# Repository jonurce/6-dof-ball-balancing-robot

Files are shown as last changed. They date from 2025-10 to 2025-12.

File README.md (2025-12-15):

# 6 Degree-of-Freedom Ball Balancing Robot 

**This project was developed as part of the course MMA4004 Mechatronics and Systems Integrations at NTNU, Ålesund**

**It was also done as a part time job, which focused on creating a reproducible project for robotics students at NTNU**

version-1
version-1-1

## Overview

This repository shows the building process of a 6 degree-of-freedom ball balancing robot. It can be used as a learning project for robotics students, as it was used for Master students in Mechatronics and Automation at NTNU, Ålesund.

## Repository Description

The repository is divided as follows:

```     
├── Arduino Code                                            # Arduino code, including the solved and not-solved versions 
├── Arduino libraries                                       # Manually installed Arduino libraries  
├── CAD files                                               # 3D files in STL format, ready for 3D printing
├── Lasercuted files                                        # Drawings for lasercuting components
├── Final Version                                           # Final version of the project for the course MMA4004
├── 6 DOF Ball Balancing Robot - Guide.pdf                  # Step by step guide to build the platform
├── 6 DOF Ball Balancing Robot - Inverse Kinematics.pdf     # Inverse Kinematics solution explanation
└── List of Materials.xlsx                                  # Component list with links
```

## Project for students

If using this repository as a project for students, it is proposed to not provide the inverse kinematics solution `6 DOF Ball Balancing Robot - Inverse Kinematics.pdf` neither the solved arduino code `Arduino Code/Arduino_Code_Solved` nor the final version `Final Version`. In addition, the document `6 DOF Ball Balancing Robot - Guide.pdf` was explicitly made for students to follow.

## Final version of the project for MMA4004

version-2
version-2-1

The final version presented for the course is available at the folder `Final Version`, which is distributed as follows:

```     
├── Final Version                                           
    ├── Code                                            # Final code
    ├── CAD_files.zip                                   # CAD files including first and second version STL files for 3D printing and drawings for lasercuting
    └── Final Report - 6 DOF Ball Balancing Robot.pdf   # Final project report
```

The final project report `Final Version/Final Report - 6 DOF Ball Balancing Robot.pdf` explains all the implemented features in detail, as well as the obtained results.

The final code is explained in details at Modesta's repository: https://github.com/ModeS7/MMA4004-stewart.git

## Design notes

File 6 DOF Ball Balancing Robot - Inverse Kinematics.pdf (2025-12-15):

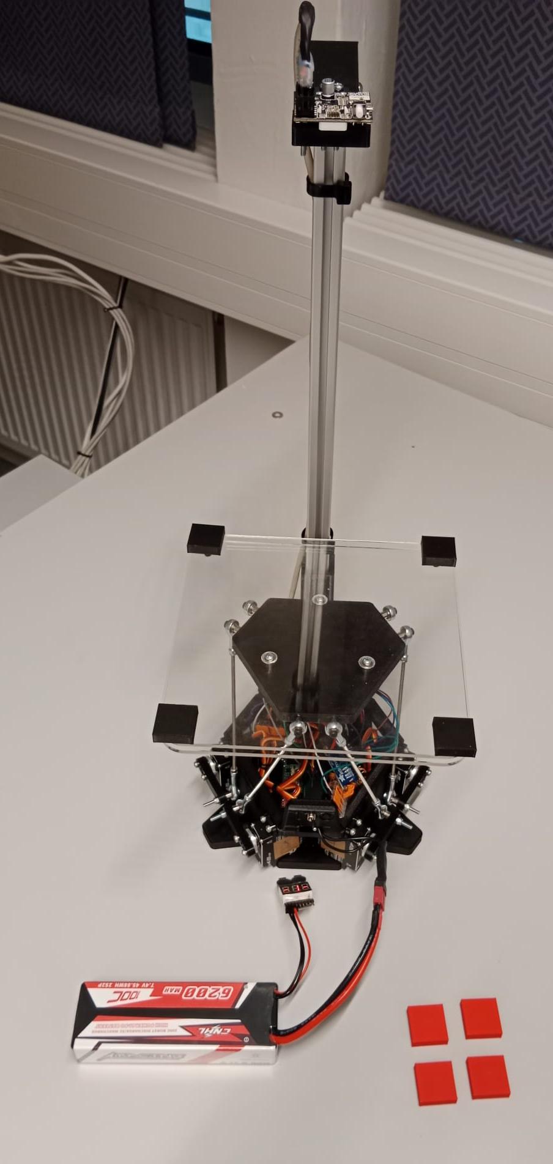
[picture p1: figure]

## 6-Degree-of-Freedom Ball Balancing Robot

Inverse Kinematics (IK)

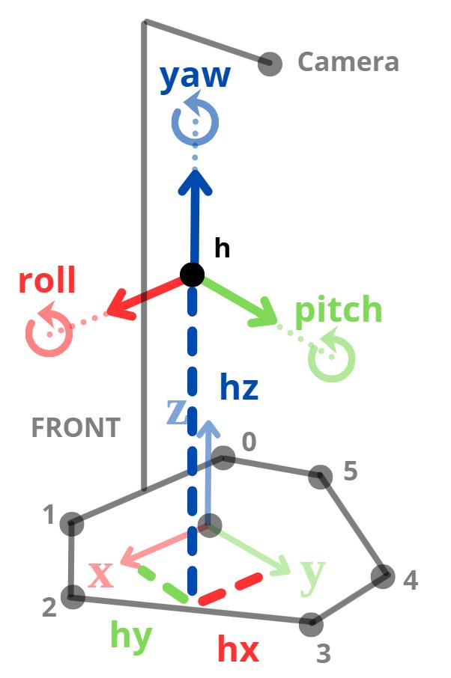
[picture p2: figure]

## IK main objetive

Given a desired h point:
h = {hx, hy, hz, roll, pitch, yaw}

Find x6 motor angles:
angles = {0, 1, 2, 3, 4, 5}

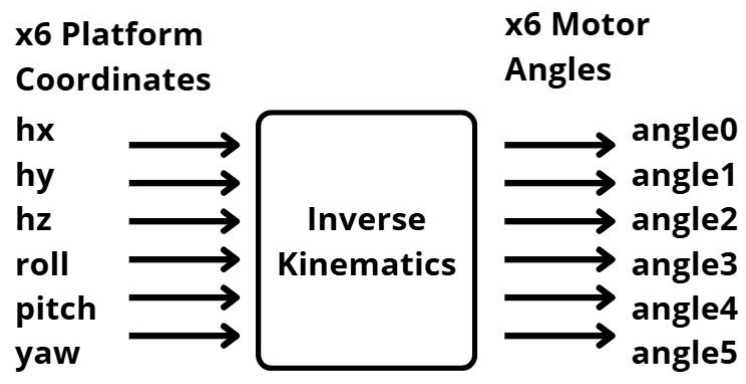
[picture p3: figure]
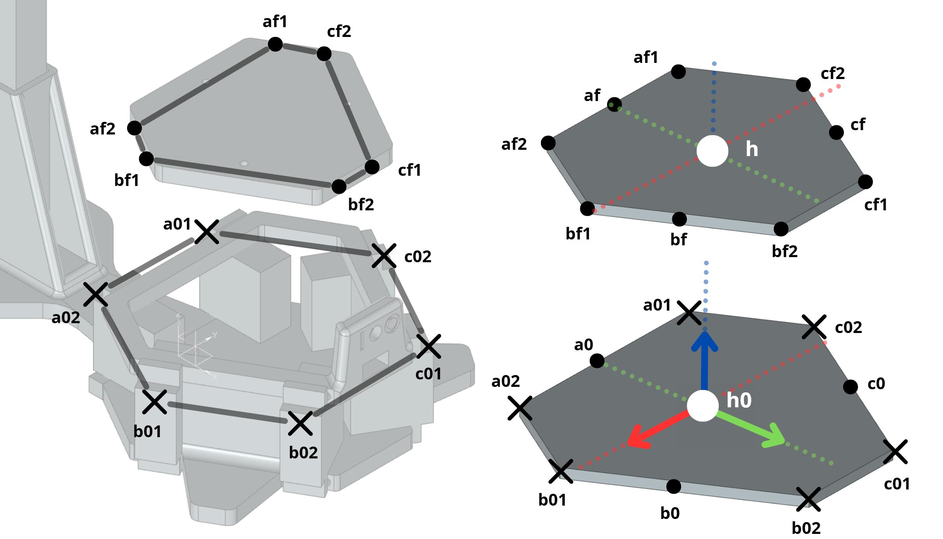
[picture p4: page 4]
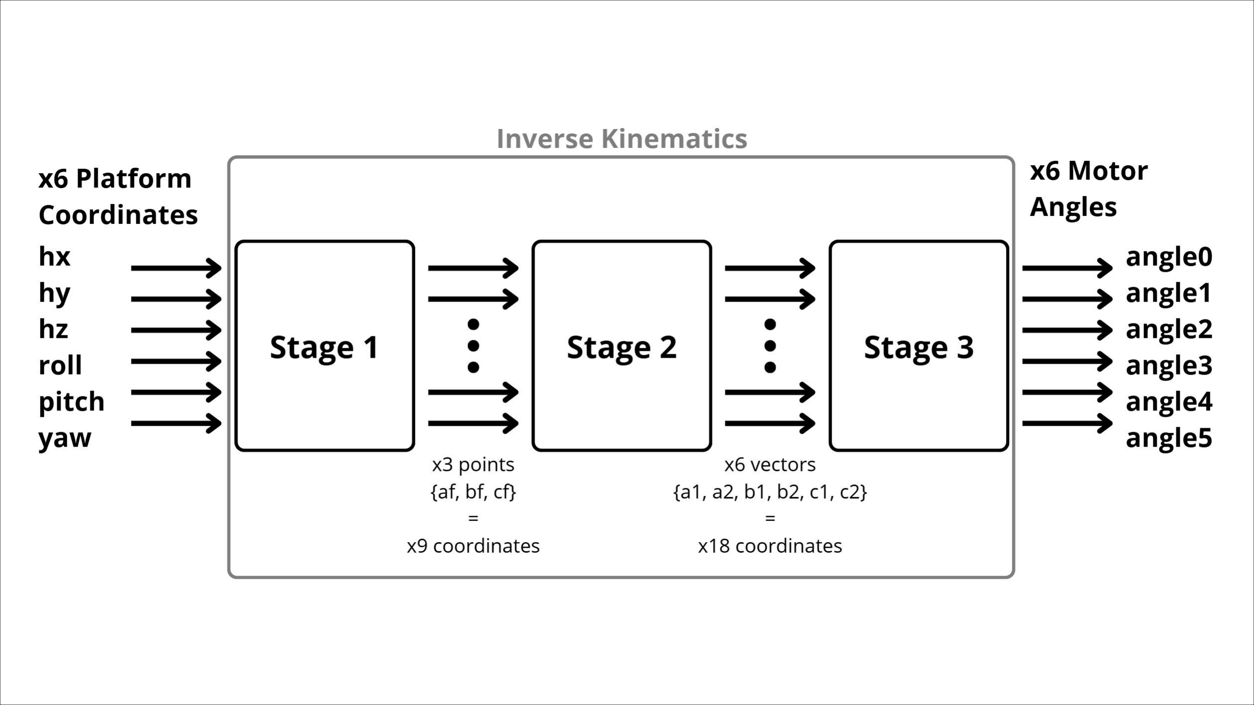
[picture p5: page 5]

## Stage 1: from h to {af, bf, cf}

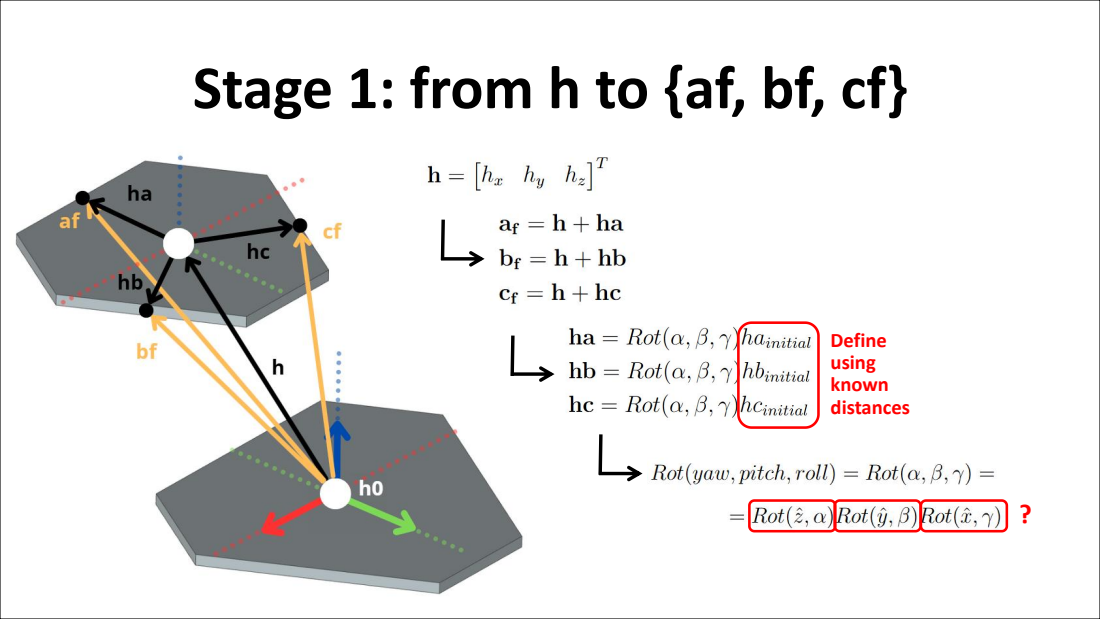
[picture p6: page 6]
Define using known distances

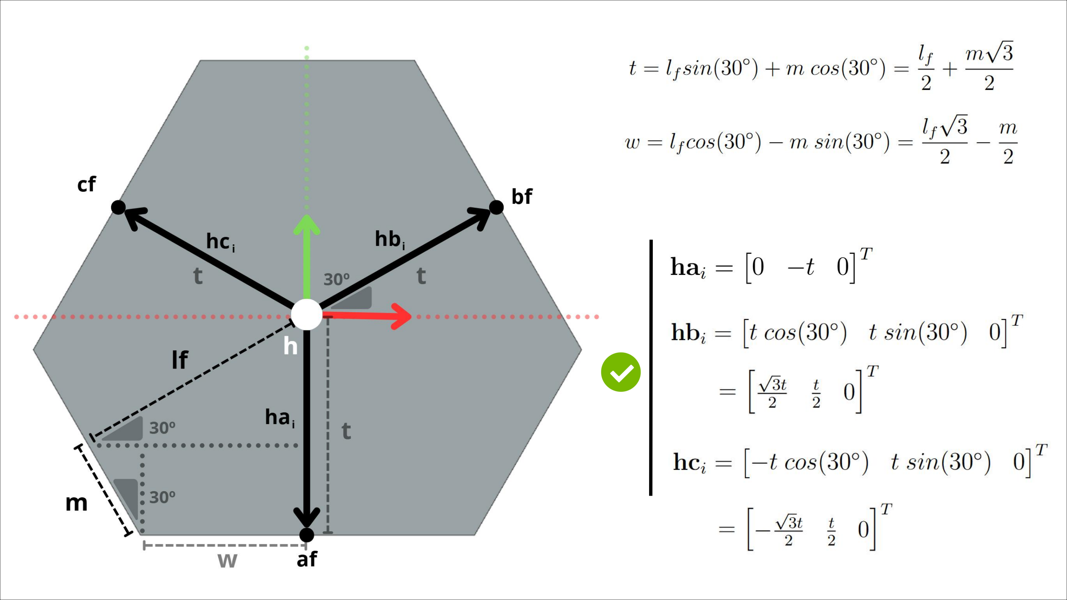
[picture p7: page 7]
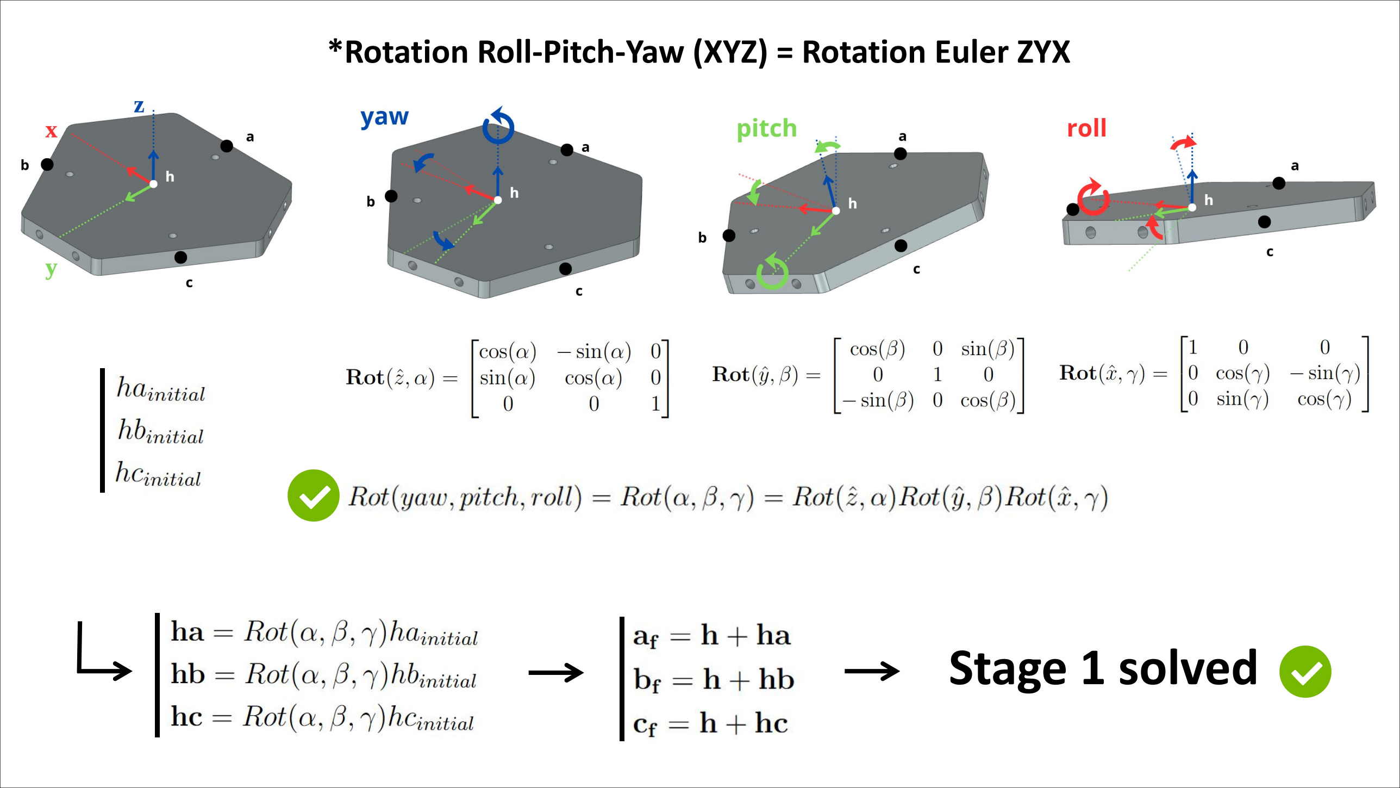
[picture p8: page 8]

Stage 1 solved

*Rotation Roll-Pitch-Yaw (XYZ) = Rotation Euler ZYX

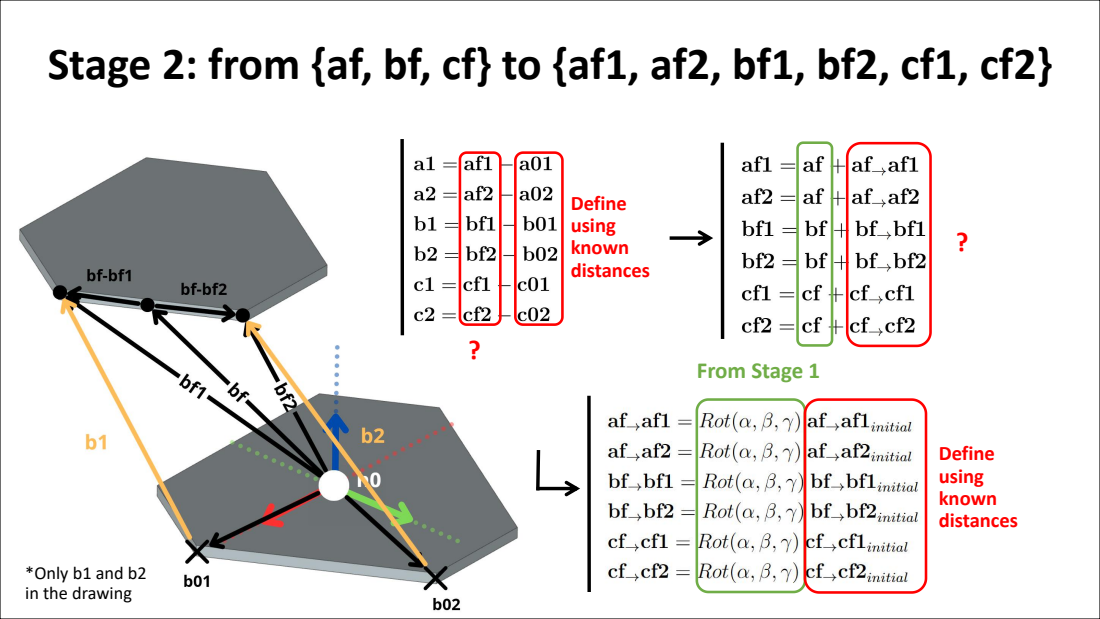
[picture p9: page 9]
From Stage 1; Define using known distances

Stage 2: from {af, bf, cf} to {af1, af2, bf1, bf2, cf1, cf2}

*Only b1 and b2
in the drawing

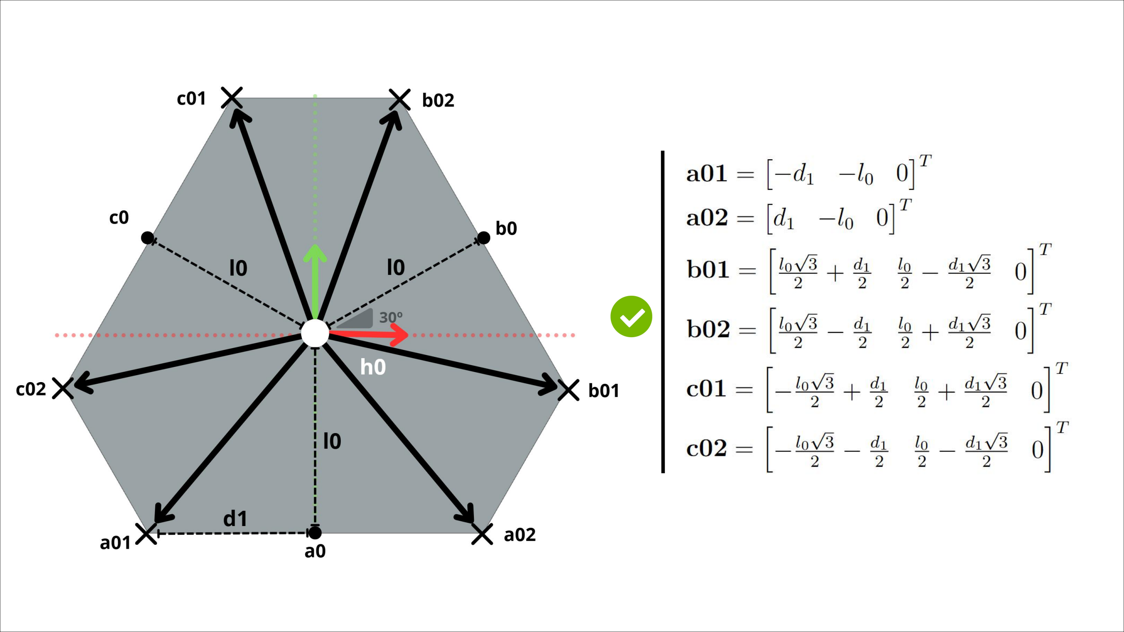
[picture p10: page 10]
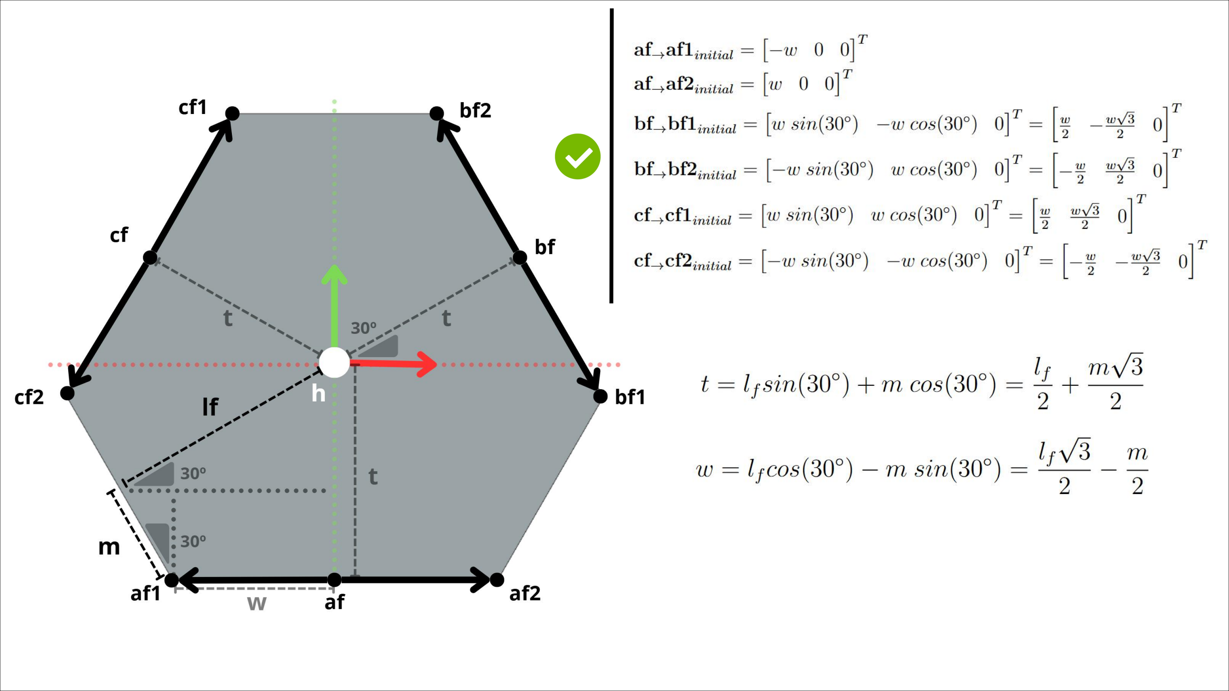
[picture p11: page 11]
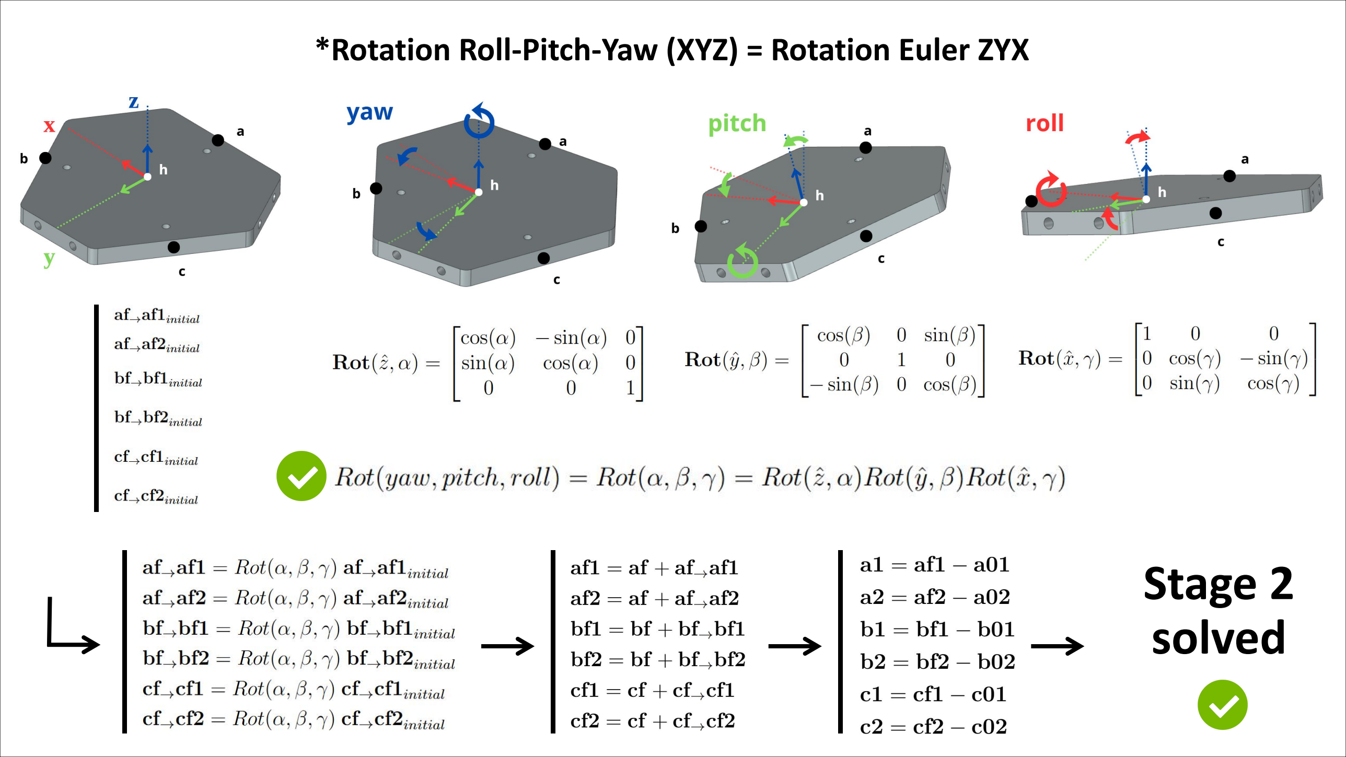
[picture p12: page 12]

*Rotation Roll-Pitch-Yaw (XYZ) = Rotation Euler ZYX

Stage 2
solved

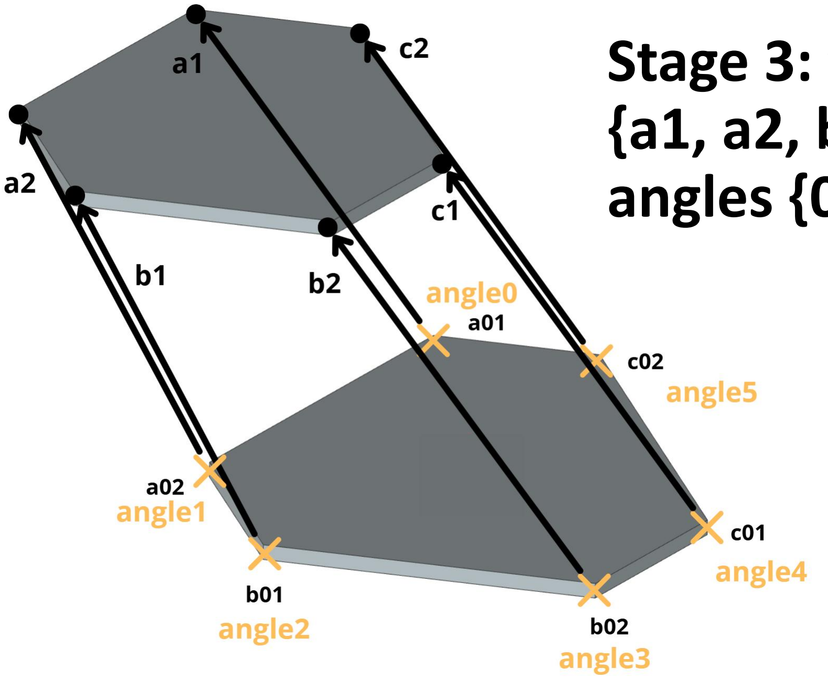
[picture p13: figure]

Stage 3: from vectors
{a1, a2, b1, b2, c1, c2} to angles {0, 1, 2, 3, 4, 5}

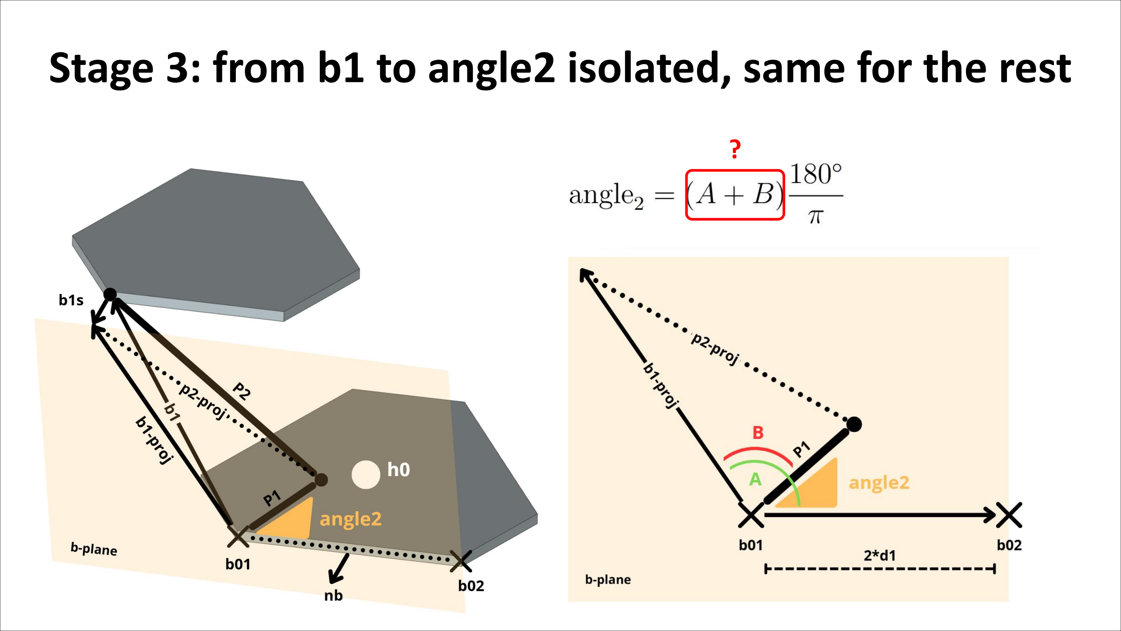
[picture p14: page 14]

Stage 3: from b1 to angle2 isolated, same for the rest

?

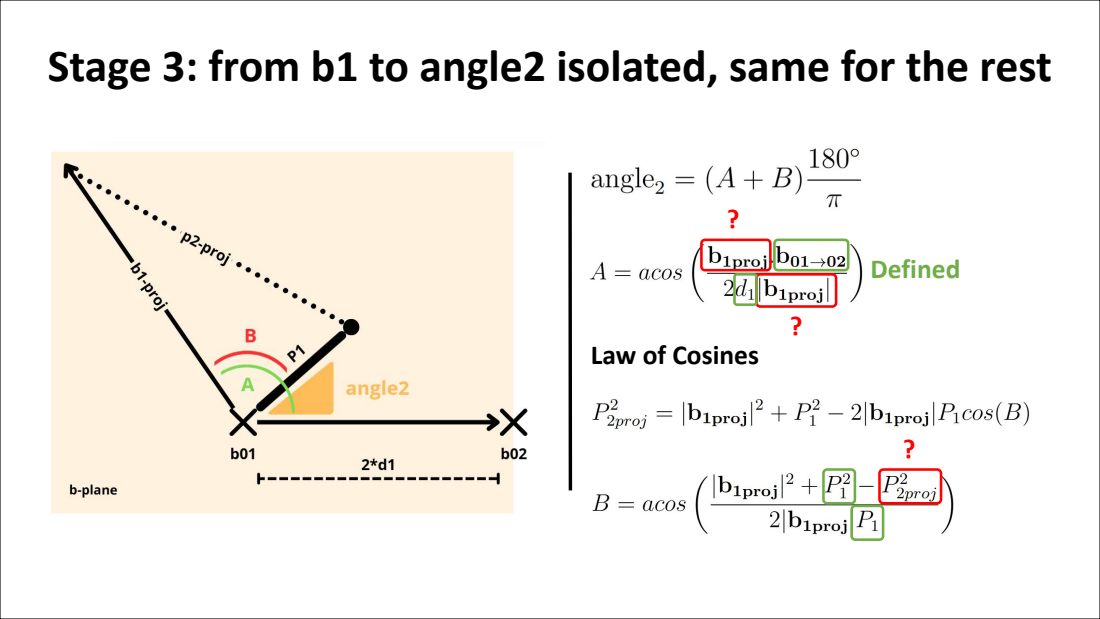
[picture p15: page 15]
Defined

Stage 3: from b1 to angle2 isolated, same for the rest

Law of Cosines

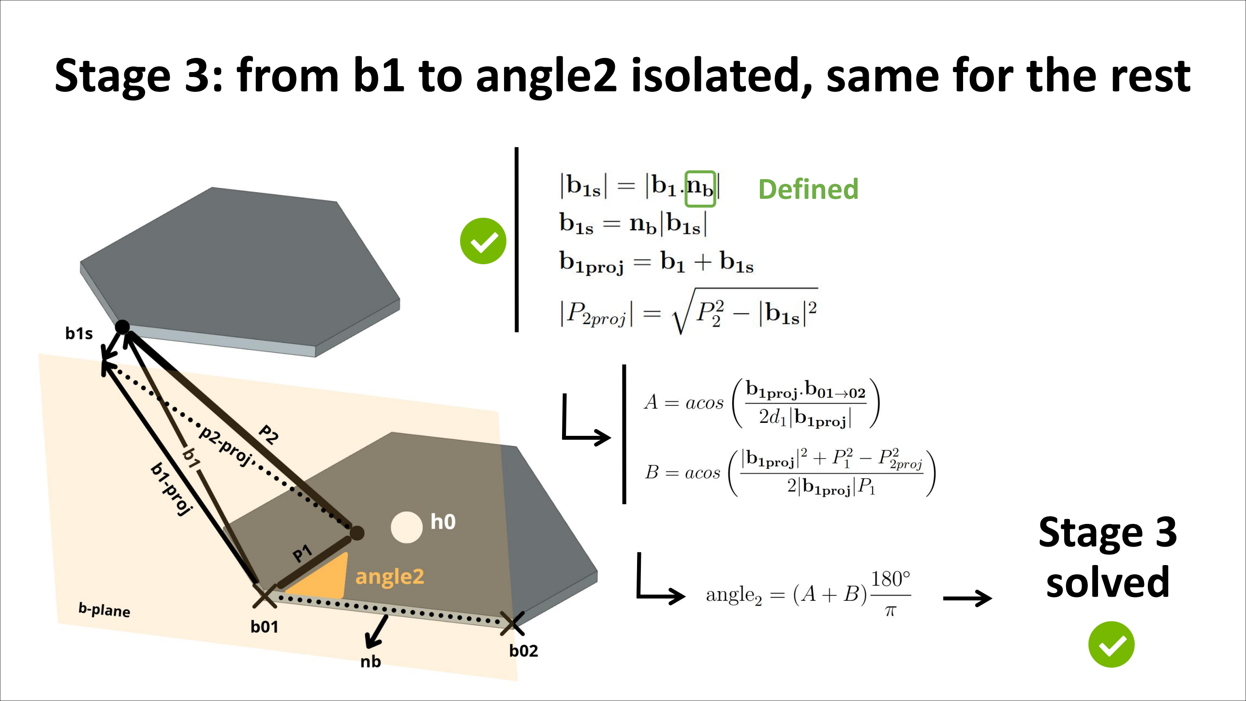
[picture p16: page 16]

Stage 3: from b1 to angle2 isolated, same for the rest

Stage 3
solved

Defined

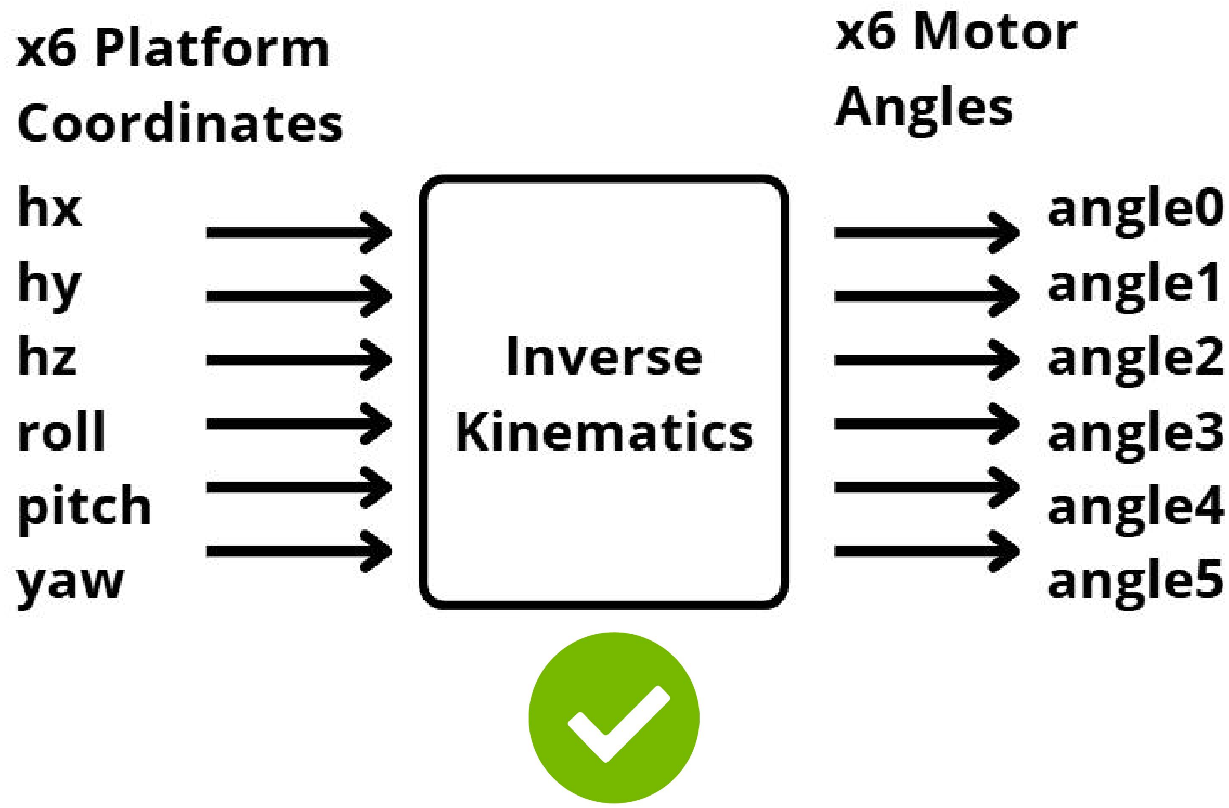
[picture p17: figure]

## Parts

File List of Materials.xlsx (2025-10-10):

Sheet: Bill of Materials
6 DOF Platform - List of components
Electronics | Units | Materials | Units
Servo Motor 20Kg 7.4V (https://www.digikey.no/en/products/detail/dfrobot/SER0030/7597225) | 6 | 3D printer filament | -
Teensy 4.1 (https://www.elfadistrelec.no/en/teensy-development-board-6v-sparkfun-electronics-dev-16771/p/30178274) | 1 | Acrylic 3mm thickness | -
Micro Maestro 6-channel USB Servo Controller (https://www.digikey.no/no/products/detail/sparkfun-electronics/09664/5764499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) | 1 | Aluminium Servo Disc | 6
Pixy 2 Camera (https://www.elfadistrelec.no/en/pixy2-cmucam5-camera-board-sparkfun-electronics-sen-14678/p/30145515) | 1 | M3 Stainless Steel Threaded Rod 1m (https://no.rs-online.com/web/p/threaded-rods/0280363) | 1
3.3V to 5V LLC (https://www.elfadistrelec.no/en/bi-directional-logic-voltage-level-converter-sparkfun-electronics-bob-12009/p/30145425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) | 1 | M3 x 6mm Inserts (https://no.rs-online.com/web/p/threaded-inserts/2040620?gb=s) | 48
Custom PCB (https://www.pcbway.com/) | 1 | M3 x 5mm Standoff (https://no.rs-online.com/web/p/standoffs/0222367?gb=s) | 22
Male Pins 1 Row for PCB (https://no.rs-online.com/web/p/pcb-headers/7671176P?gb=s) | 84 | M3 Locknuts (https://no.rs-online.com/web/p/hex-nuts/0767804?gb=s) | 24
Female Pins 1 Row for PCB (https://no.rs-online.com/web/p/pcb-sockets/7655806?gb=s) | 80 | M3 x 5mm Screws (https://no.rs-online.com/web/p/socket-screws/8229094?gb=s) | 24
Male-female/male-male wire | 6 | M3 x 14mm Screws (https://no.rs-online.com/web/p/socket-screws/0606457?gb=s) | 30
2-Contact Screw Termination (https://no.rs-online.com/web/p/pcb-terminal-blocks/1468345?gb=s) | 1 | M3 x 20mm Button Head Screw (https://no.rs-online.com/web/p/security-screws/6212760?gb=s) | 3
USB cable | 2 | M3 x 25mm Screw (https://no.rs-online.com/web/p/socket-screws/0293319?gb=s) | 9
3x2 Male Pins (https://no.rs-online.com/web/p/pcb-headers/1802895) | 1 | 20 x 20mm Alum Profile 5mm Groove 2m (https://no.rs-online.com/web/p/tubing-and-profile-struts/8508470?gb=s) | 1.2
3x2 Female Pins (https://no.rs-online.com/web/p/pcb-sockets/2079182?gb=s) | 2 | M5 T-Slot Nut Groove Size 5mm (https://no.rs-online.com/web/p/connecting-components/1809104) | 8
Toggle Switch (https://www.elfadistrelec.no/en/miniature-toggle-switch-on-off-on-1co-soldering-lugs-rs-pro-7347123/p/30466736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) | 1 | M5 x 12mm Screw (https://no.rs-online.com/web/p/socket-screws/0281079?gb=s) | 8
18 AWG Wire | 40cm | Silicon Glue Tube (https://no.rs-online.com/web/p/glues/7703434?gb=s) | 1
Amass T-Plug2 [deans] - 1x Male (https://www.elkjop.no/product/hjem-rengjoring-og-kjokkenutstyr/belysning-og-elektriske-artikler/elektrisk-utstyr/kabler-og-adaptere/amass-t-plug2-deans-1x-mal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) | 1
LiPo Battery 7.4V 6200mAh (https://www.elkjop.no/product/sport-hobby-og-fritid/leker/radiostyrte-kjoretoy-og-tilbehor/reservedeler-til-radiostyrte-kjoretoy/2s-6200mah-100c-cnhl-racing-s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) | 1
Cable x5 cores (https://no.rs-online.com/web/p/control-cable/2658824?gb=s) | 80cm
Cable Nylon Cover | 5cm
LiPo Alarm (https://www.elefun.no/vare-33067/radioutstyr-tilbehor-buzzer-2s-8s-lipo-alarm-voltage-tester) | 1
Voltage Regulator 5V (https://uk.rs-online.com/web/p/voltage-regulators/5339404) | 1

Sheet: Pre Bill of Material
 | Stewart Platform
 | Name of Component | Price | Sold Quantity | Needed Quantity | Cost of Used Parts
 | Electronics
Ordered | JX CLS6336HV 35kg digital servo (https://www.amazon.com/dp/B087LQXDS9?psc=1&ref=ppx_yo2ov_dt_b_product_details) | $33.89 | 1 | 6 | $203.34
 | Teensy 4.1 (https://www.amazon.com/dp/B088D3FWR7?psc=1&ref=ppx_yo2ov_dt_b_product_details) | $41.99 | 1 | 1 | $41.99
 | 6 channel Polulu Maestro servo controller (https://www.amazon.com/dp/B004G54CHW?psc=1&ref=ppx_yo2ov_dt_b_product_details) | $40.96 | 1 | 1 | $40.96
 | Pixy2 Camera (https://www.amazon.com/Charmed-Labs-Pixy2-Vision-Sensor/dp/B07D1CLYD2) | $69.90 | 1 | 1 | $69.90
pins in lab | 3.3 to 5v logic level converter (https://www.amazon.com/dp/B07F7W91LC?psc=1&ref=ppx_yo2ov_dt_b_product_details) | $7.49 | 10 | 1 | $0.75
From lab | half proto board+screw terminal (https://www.amazon.com/dp/B08BWPGSSC?psc=1&ref=ppx_yo2ov_dt_b_product_details) | $13.99 | 6 | 1 | $2.33
 | SPST switch (https://www.amazon.com/dp/B01N2U8PK0?psc=1&ref=ppx_yo2ov_dt_b_product_details) | $6.99 | 15 | 1 | $0.47
 | 18 AWG wire (https://www.amazon.com/BNTECHGO-Silicone-Flexible-Strands-Stranded/dp/B01C5CANVG?s=industrial) | $13.98 | 1 | 1 | $13.98
 | XT60H connector pair (https://www.amazon.com/Upgrade-Female-Bullet-Connectors-Battery/dp/B07VRZR5TL) | $7.99 | 12 | 1 | $0.67
 | 2S (7.4v) 6200mah lipo battery (https://www.amazon.com/Zeee-6200mAh-Battery-Connector-Evader/dp/B07YD6282M) | $24.99 | 1 | 1 | $24.99
 |  |  |  | Subtotal | $399.37
 | Material
In lab (20% infill - ball 100%) | 3D printer filament | $25.00 | 1000 | 183
In lab (3mm thick) | Platform (https://www.andymark.com/products/waterjet-cutting-services?sku=am-waterjetservice) | $8.99 | 1 | 1
 | 25T servo disc (https://www.amazon.com/Seamuing-Aluminum-Futaba-Mechanical-Helicopter/dp/B07D56FVK5) | $10.99 | 10 | 6 | $6.59
 | m3 x 120mm pushrod connector (https://www.amazon.com/dp/B07MC44S4T?ref=ppx_yo2ov_dt_b_product_details&th=1) | $12.49 | 10 | 6 | $7.49
Missing | 22mm long m3 tie rod (https://www.amazon.com/dp/B09JLKLK73?psc=1&ref=ppx_yo2ov_dt_b_product_details) | $11.99 | 10 | 12 | $14.39
 | m3 x 6mm threaded inserts (https://www.amazon.com/dp/B07LBQRYR3?psc=1&ref=ppx_yo2ov_dt_b_product_details) | $9.49 | 50 | 36 | $6.83
 | m3 x 10mm standoffs (https://www.amazon.com/dp/B07M7D8LC8/ref=twister_B086M869HG?_encoding=UTF8&th=1) | $9.99 | 10 | 3 | $3.00
 | m3 x 5mm standoffs (https://www.amazon.com/dp/B07M7D9PRM?psc=1&ref=ppx_yo2ov_dt_b_product_details) | $7.49 | 10 | 14 | $10.49
 | m3 locknuts (https://www.amazon.com/100Pcs-Stainless-Self-Lock-Inserted-Clinching/dp/B075ZZW7VL?s=hi) | $6.99 | 100 | 24 | $1.68
 | m3 x 5mm screws (https://www.amazon.com/iExcell-Socket-Screws-Bolts-Finish/dp/B08B1T4HHP) | $6.58 | 100 | 24 | $1.58
 | m3 x 10mm screws (https://www.amazon.com/iExcell-Socket-Screws-Bolts-Finish/dp/B0BCG79KG4) | $6.68 | 100 | 2 | $0.13
 | m3 x 12mm screws (https://www.amazon.com/iExcell-Socket-Screws-Bolts-Finish/dp/B08B1W1FHS) | $6.78 | 100 | 18 | $1.22
use 15 mm | m3 x 14mm screws (https://www.amazon.com/iExcell-Socket-Screws-Bolts-Finish/dp/B08B1VN3BJ) | $6.88 | 100 | 6 | $0.41
 | m3 x 15mm screws (https://www.amazon.com/iExcell-Stainless-Socket-Screws-Wrench/dp/B089KTD5G3) | $7.28 | 100 | 4 | $0.29
from lab | m3 x 20mm button head screws (https://www.amazon.com/M3-0-5-Button-Socket-Stainless-Quantity/dp/B083HCWJGQ) | $9.49 | 100 | 3
from lab 25mm | m3 x 22mm screws (https://www.amazon.com/Electronics-Salon-100pcs-Machine-Combination-Phillips-Slotted/dp/B06ZZ1LLQ7) | $10.99 | 100 | 6
 | m3 x 30mm screws (https://www.amazon.com/iExcell-Stainless-Socket-Button-Screws/dp/B08H2JKBCN) | $6.68 | 50 | 3 | $0.40
Missing | 3/4 x 48 inch wooden dowel (https://www.amazon.com/Inch-Wooden-Dowel-Rods-Woodworking/dp/B01GQTB99Y) | $26.19 | 1 | 1
 | #6 x 1-1/4 inch wood screws (https://www.amazon.com/Stainless-Phillips-Tapping-SG-TZH/dp/B09C5FM888) | $9.99 | 100 | 4
 |  |  |  | Subtotal | $54.51
 |  |  |  | Total | $453.88

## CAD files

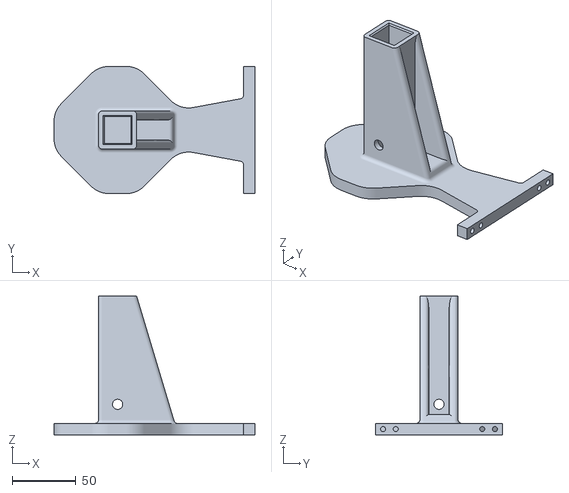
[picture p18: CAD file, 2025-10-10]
CAD files/CamBottom.stl
158.0 x 100.0 x 109.0

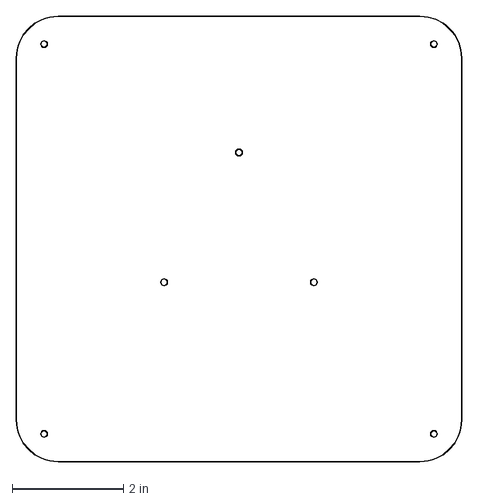
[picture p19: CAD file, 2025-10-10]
Lasercuter files/platform.dxf
8.00 x 8.00 in

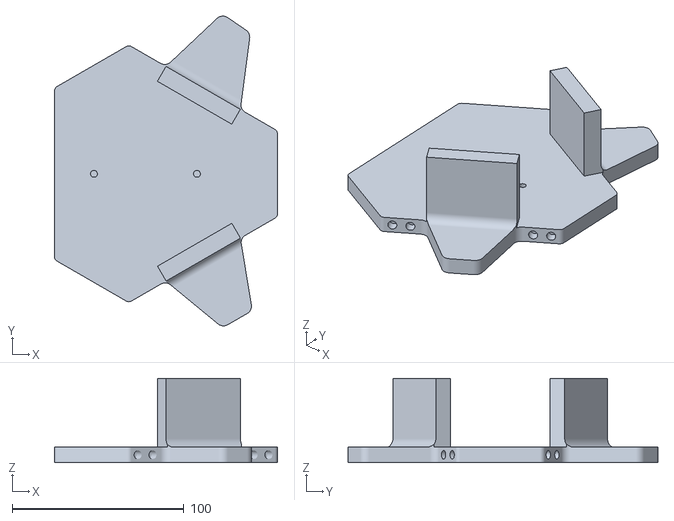
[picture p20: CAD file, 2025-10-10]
CAD files/BaseBottom.stl
129.9 x 180.4 x 49.0

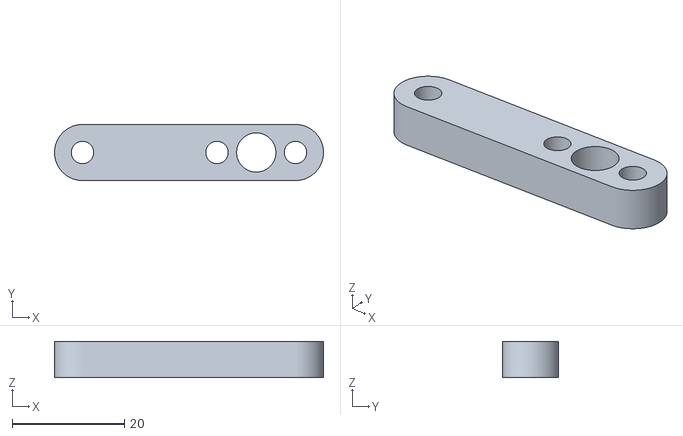
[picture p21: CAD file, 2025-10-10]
CAD files/MotorArm_x6.stl
48.0 x 10.0 x 6.50

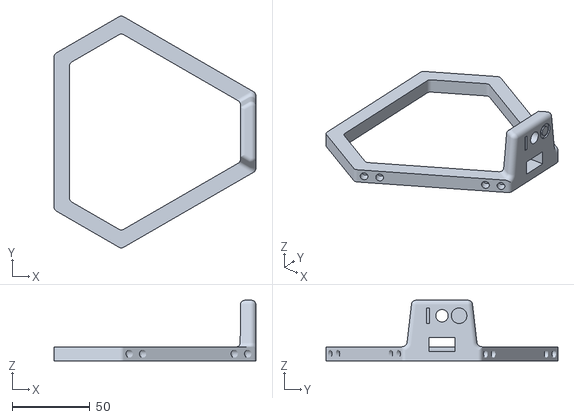
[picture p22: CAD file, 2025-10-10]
CAD files/BaseTop.stl
129.9 x 149.1 x 39.0

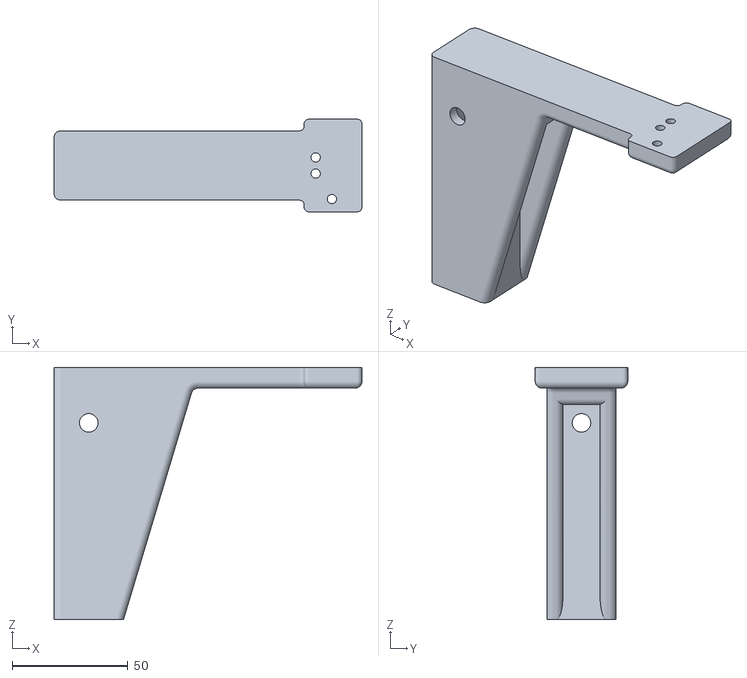
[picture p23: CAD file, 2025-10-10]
CAD files/CamTop.stl
133.0 x 40.0 x 109.0

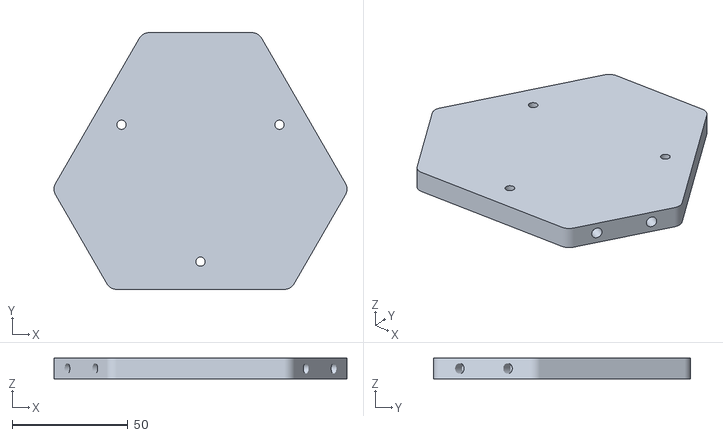
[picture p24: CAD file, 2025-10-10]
CAD files/PlatformBase.stl
126.5 x 110.9 x 9.00

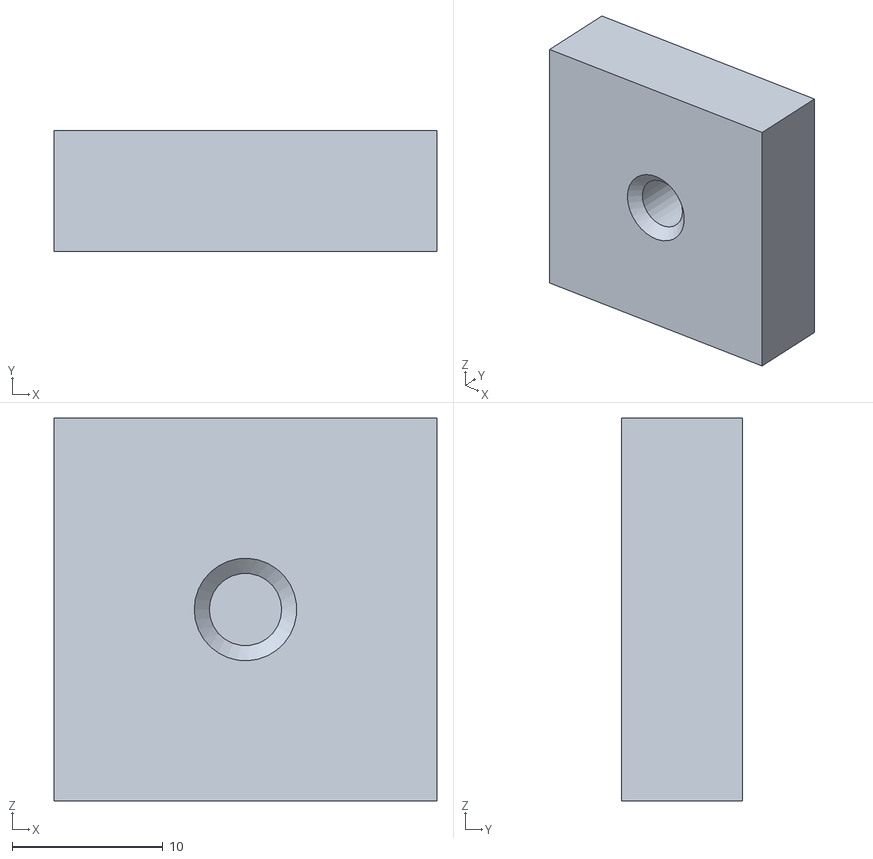
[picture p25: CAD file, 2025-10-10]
CAD files/CenterMarker_x4.stl
25.4 x 8.00 x 25.4

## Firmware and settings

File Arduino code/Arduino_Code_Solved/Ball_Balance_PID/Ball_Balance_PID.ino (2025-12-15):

/*               ****NOTES****
  Before using this, go to the Serial Settings
  tab in the Maestro Control Center and apply these settings:

   Serial mode: UART, fixed baud rate
   Baud rate: 9600
   CRC disabled

  Be sure to click "Apply Settings" after making any changes.

  Array Indexes
  -------------
  a1 = 0
  a2 = 1
  b1 = 2
  b2 = 3
  c1 = 4
  c2 = 5

  range for hz (105, 140)

*/

// libraries
#include "PololuMaestro.h"
#include "math.h"
#include <Pixy2SPI_SS.h>

#define maestroSerial SERIAL_PORT_HARDWARE_OPEN  //for teensy

// --------------------------------------------------
// ------------------- START TUNE -------------------

// TUNE: ANGLE OFFSET FOR EACH MOTOR [NEGATIVE UP / POSITIVE DOWN] - DEGREES
// *should be less than 14 degrees since there are 25 teeth on the servo
float offset[6] = { -0.5, 7,    // channel #0 and channel #1
                    -2, 4,    // channel #2 and channel #3
                    -2.5, 5.5 };  // channel #4 and channel #5

// TUNE: INPUTS FROM CAMERA CALIBRATION
float origin[2] = { 160, 108 };  // (144, 108) X and Y co-ords of the  (in the camera frame)
float r_platform = 115;   // (121) distance from the center of the platform to the corner of the platform seen from the pixy2 cam


// TUNE: HOME hx, hy, hz, roll, pitch, yaw
float hx_home = 0;
float hy_home = 0;
float hz_home = 120;// 118.19374266158451;
float roll_home = 0;
float pitch_home = 0;
float yaw_home = 0;

// TUNE: MAX AVERAGE ANGLE CHANGE (PITCH AND ROLL) IN ONE STEP - DEGREES
float r_max = 15;  

// TUNE: PID CONSTANTS VALUES
float kp = -0.05;         // proportional constant 6e-4
float kd = -0.05;         // derivative constant 0.56
float ki = 0;         // integral constant

// TUNE: Low pass filter constant T
float T = 0.08;

// TUNE: MOTOR VELOCITIES AND ACCELERATIONS
int vel_home = 20;
int acc_home = 20;
int vel_control = 0;
int acc_control = 0;

// TUNE: INPUTS FROM MEASUREMENTS (mm)
float l0 = 73.025; // from h0 to a0
float d1 = 36.8893; // from a0 to a01
float lf = 67.775; // from hf to midle af1-cf2
float m = 12.7; // from previous middle point to af1
float p1 = 31.75; // motor small arm
float p2 = 129; // motor long arm

// ------------------- END TUNE -------------------
// ------------------------------------------------


// **OBJECTS**
Pixy2SPI_SS pixy;
MicroMaestro maestro(maestroSerial);  // if using the Maestro Micro controller

//**CONSTANTS**
float abs_0 = 4000;                                     //ms position of absolute 0 degrees
float abs_90 = 8000;                                    //ms position of absolute 90 degrees
float toDeg = 180 / PI;                                 // radians to degrees conversion factor
float toRad = 1 / toDeg;
int x = 0, y = 1, z = 2;                                // defines x, y, and z array indexes to be used
String ID[6] = { "a1", "a2", "b1", "b2", "c1", "c2" };  //servo ID's

// ANGLE RANGE FOR EACH SERVO CCW
// each servo can move from absolute 0 to absolute 90 degrees
// this defines a different range such as 90 to 180 degrees
float range[6][2] = { { -45, 45 }, { 45, -45 },  // a1, a2
                      { -45, 45 }, { 45, -45 },  // b1, b2
                      { -45, 45 }, { 45, -45 }};  // c1, c2


//**INVERSE KINEMATICS**

// calculates points a10, a20, b10, b20, c10, and c20
float a10[3] = { -d1, -l0, 0 };
float a20[3] = { -a10[x], a10[y], 0 };
float b10[3] = { l0*sqrt(3.0f)/2.0f + d1/2.0f, l0/2.0f - d1*sqrt(3.0f)/2.0f, 0 };
float b20[3] = { l0*sqrt(3.0f)/2.0f - d1/2.0f, l0/2.0f + d1*sqrt(3.0f)/2.0f, 0 };
float c10[3] = { -b20[x], b20[y], 0 };
float c20[3] = { -b10[x], b10[y], 0 };

// calculates vectors a_10_20, b_10_20, c_10_20,
float a_10_20[3] = { a20[x] - a10[x], a20[y] - a10[y], a20[z] - a10[z] };
float b_10_20[3] = { b20[x] - b10[x], b20[y] - b10[y], b20[z] - b10[z] };
float c_10_20[3] = { c20[x] - c10[x], c20[y] - c10[y], c20[z] - c10[z] };

//calculates normal vectors na, nb, and nc for each side of the triangle
float na[3] = { 0, -1, 0 }; // pointing out
float nb[3] = { sqrt(3.0f)/2.0f, 1/2.0f, 0 }; // pointing out
float nc[3] = { -sqrt(3.0f)/2.0f, 1/2.0f, 0 }; // pointing out

float t = lf/2.0f + m*sqrt(3.0f)/2.0f;
float w = lf*sqrt(3.0f)/2.0f - m/2.0f;

// calculated theta values a1, a2, b1, b2, c1, c2 respectively
float theta[6];                      
float theta_prev[6];

// **PIXY2 CAMERA**
float ball[2];// X and Y co-ords of the ball

// **PID**
float error[2];       // error of the ball
float error_prev[2];  // previous error value used to calculate derivative. Derivative = (error-previous_error)/(change in time)
float deriv[2] = {0,0};     // Initialize derivative of the error
float integral[2] = {0, 0}; // Initialize integral (x, y components)
float out[2];         // output values (pitch and roll) in degrees
float time_i;         // initial time
float time_f;         // final time
float delta_time;     // change in time (rename from 'time')

void setup() {
  Serial.begin(115200);
  // maestroSerial.begin(9600);
  // maestroSerial.begin(115200);
  maestroSerial.begin(250000);
  pixy.init();
}

void loop() {
  findBall();  // finds the location of the ball
  if (ball[x] == 4004 && ball[y] == 4004) {
    // sees if ball position (x and y) is 4004, if so then the ball is not detected and platform should be in home position
    InverseKinematics(hx_home, hy_home, hz_home, roll_home, pitch_home, yaw_home);  //hx, hy, hz, roll, pitch, yaw
    moveServos(vel_home, acc_home);
  } else {
    PID();  // calculates the proportional and derivative terms and outputs them to the platform
  }
}


// move servo i to an input position at a certain speed and acceleration value
void moveServo(int i, float pos, int spd, int acc) {        
  pos = pos + offset[i];                                    //adds offset amount to the input position (degrees)
  pos = map(pos, range[i][0], range[i][1], abs_0, abs_90);  //converts input pos to ms position
  maestro.setSpeed(i, spd);                                 //sets input speed to servo i
  maestro.setAcceleration(i, spd);                          //sets input acceleration to servo i
  maestro.setTarget(i, pos);                                //drives motor to calculated position
}

//moves all servos to their calculated positions at a certain speed and acceleration value
void moveServos(int spd, int acc) {  
  float pos;
  for (int i = 0; i < 6; i++) {
    maestro.setSpeed(i, spd);                                 //sets input speed to servo i
    maestro.setAcceleration(i, acc);                          //sets input acceleration to servo i
    pos = theta[i] + offset[i];                               //adds offset amount to the calculated angle (degrees)
    pos = map(pos, range[i][0], range[i][1], abs_0, abs_90);  //converts input pos to ms position
    maestro.setTarget(i, pos);                                //drives motor to calculated position
  }
}

//ends the program and stops all of the servos
void stop() {  
  for (int i = 0; i < 6; i++) {
    maestro.setTarget(i, 0);  //stops servo i
  }
  while (1) {}
}

// find the location of the ball using the pixy2 cam
void findBall() {  
  // grab blocks!
  pixy.ccc.getBlocks();

  // If there is 1 ball detected then collect and print the data
  if (pixy.ccc.numBlocks == 1) {
    //sets current X and Y co-ords
    ball[x] = pixy.ccc.blocks[0].m_x;  // absolute X location of the ball
    ball[y] = pixy.ccc.blocks[0].m_y;  // absolute Y location of the ball
  }
  // If there are multiple balls detected, then print so
  else if (pixy.ccc.numBlocks > 1) {
    Serial.println("MULTIPLE BALLS DETECTED");
    ball[x] = 4004;  // X component of the ball
    ball[y] = 4004;  // Y component of the ball
  }
  // If there is no ball detected, then print so
  else {
    // Serial.println("NO BALL DETECTED");
    ball[x] = 4004;  // X component of the ball
    ball[y] = 4004;  // Y component of the ball
  }
}

// calculates the Proportional, Derivative an Integral values and moves the servos
void PID() {  
 
  // the error is a vector pointing from the center of the platform to the center of the ball
  error[x] = ball[x] - origin[x];  // x component of error (origin x-axis and camera x-axis are the same)
  error[y] = -(ball[y] - origin[y]);  // y component of error (origin y-axis and camera y-axis are opposite)

  time_f = millis();             // sets final time
  delta_time = (time_f - time_i) / 1000;  // change in time (seconds)
  time_i = millis(); // sets initial time

  // x and y components of derivative with low-pass filter  
  deriv[x] = deriv[x] + delta_time/T*( -deriv[x] + (error[x] - error_prev[x]) / delta_time ); 
  deriv[y] = deriv[y] + delta_time/T*( -deriv[y] + (error[y] - error_prev[y]) / delta_time ); 

  // Trapezoidal rule for integral values of x and y
  integral[x] += (error[x] + error_prev[x]) * delta_time / 2.0; 
  integral[y] += (error[y] + error_prev[y]) * delta_time / 2.0; 

  // checks if derivative is NaN or INF. If so, set to zero
  if (isnan(deriv[x]) || isinf(deriv[x])) {  // x component of derivative
    deriv[x] = 0;
  }
  if (isnan(deriv[y]) || isinf(deriv[y])) {  // y component of derivative
    deriv[y] = 0;
  }

  // sets previous error to current error
  error_prev[x] = error[x];  // x component of previous error
  error_prev[y] = error[y];  // x component of previous error


  float r_ball = sqrt(pow(error[x], 2) + pow(error[y], 2));  // calculates the distance from the center of the platfrom to the ball
  
  // if ball to far away from center, out of the platform -> move to home position
  if (r_ball > r_platform) {
    Serial.println("Detected ball out of platform");
    InverseKinematics(hx_home, hy_home, hz_home, roll_home, pitch_home, yaw_home);  //hx, hy, hz, roll, pitch, yaw
    moveServos(vel_home, acc_home);
  }
  // if ball is inside the platform -> PID control -> set thetas to move the motors
  else {  
    out[x] = error[x] * kp + deriv[x] * kd + integral[x] * ki;
    out[y] = error[y] * kp + deriv[y] * kd + integral[y] * ki;

    // error prevention
    float r_out = sqrt(pow(out[x], 2) + pow(out[y], 2));  //calculates average of the out angle (pitch and roll)
    Serial.println(r_out);
    // if r_out is greater than r_max, then scale down out values
    if (r_out > r_max) {   
      out[x] = out[x] * (r_max / r_out);
      out[y] = out[y] * (r_max / r_out);
    }

    // compute thetas with IK
    Serial.println("Performing PID control");
    // out[x] proportional to x-axis -> to achieve linear movement in x(+) -> pitch(+) rotation
    // out[y] proportional to y-axis -> to achieve linear movement in y(+) -> roll(-) rotation
    InverseKinematics(hx_home, hy_home, hz_home, roll_home - out[y], pitch_home + out[x], yaw_home);  //hx, hy, hz, roll, pitch, yaw
    
    // move platform
    moveServos(vel_control, acc_control);
  }
}

// compute inverse kinematics
void InverseKinematics(float hx, float hy, float hz, float roll, float pitch, float yaw) { 
  // calculates theta values given hx, hy, hz, roll, pitch, yaw
  
  //-------------------------
  // **STAGE 1 CALCULATIONS**
  // From {hx, hy, hz, roll, pitch, yaw} => get {ax, ay, az; bx, by, bz; cx, cy, cz}
  //-------------------------

  // define point h (center point of platform)
  float h[3] = { hx, hy, hz }; 

  // define rotation matrices for yaw, pitch and roll
  float R_z_yaw[3][3] = {{cos(yaw * toRad), -sin(yaw * toRad), 0}, {sin(yaw * toRad), cos(yaw * toRad), 0}, {0, 0, 1}}; // row, row, row
  float R_y_pitch[3][3] = {{cos(pitch * toRad), 0, sin(pitch * toRad)}, {0, 1, 0}, {-sin(pitch * toRad), 0, cos(pitch * toRad)}}; 
  float R_x_roll[3][3] = {{1, 0, 0}, {0, cos(roll * toRad), -sin(roll * toRad)}, {0, sin(roll * toRad), cos(roll * toRad)}};

  // define initial ha, hb, and hc
  float ha_i[3] = {0, -t, 0};
  float hb_i[3] = {sqrt(3.0f)*t/2.0f, t/2.0f, 0};
  float hc_i[3] = {-sqrt(3.0f)*t/2.0f, t/2.0f, 0};

  // initialize rotated ha, hb, hc
  float ha[3] = {0, 0, 0};
  float hb[3] = {0, 0, 0};
  float hc[3] = {0, 0, 0};
  
  // calculate rotated ha, hb, hc
  rotations(ha, ha_i, R_z_yaw, R_y_pitch, R_x_roll);
  rotations(hb, hb_i, R_z_yaw, R_y_pitch, R_x_roll);
  rotations(hc, hc_i, R_z_yaw, R_y_pitch, R_x_roll);

  // calculate af, bf, cf
  float af[3] = {h[0] + ha[0], h[1] + ha[1], h[2] + ha[2]};
  float bf[3] = {h[0] + hb[0], h[1] + hb[1], h[2] + hb[2]};
  float cf[3] = {h[0] + hc[0], h[1] + hc[1], h[2] + hc[2]};
  

  //-------------------------
  // STAGE 2 CALCULATIONS
  // From {ax, ay, az, bx, by, bz, cx, cy, cz}
  // => get {a1fx, a1fy, a1fz; a2fx, a2fy, a2fz; b1fx, b1fy, b1fz; b2fx, b2fy, b2fz; c1fx, c1fy, c1fz; c2fx, c2fy, c2fz}
  //-------------------------

  // define initial vectors af_a1f, af_a2f, bf_bf1, bf_b2f, cf_c1f, cf_c2f
  float af_a1f_i[3] = {-w, 0, 0};
  float af_a2f_i[3] = {w, 0, 0};
  float bf_b1f_i[3] = {w/2.0f, -w*sqrt(3.0f)/2.0f, 0};
  float bf_b2f_i[3] = {-w/2.0f, w*sqrt(3.0f)/2.0f, 0};
  float cf_c1f_i[3] = {w/2.0f, w*sqrt(3.0f)/2.0f, 0};
  float cf_c2f_i[3] = {-w/2.0f, -w*sqrt(3.0f)/2.0f, 0};
  

  // initialize rotated vectors a1f, a2f, b1f, b2f, c1f, c2f
  float af_a1f[3] = {0, 0, 0};
  float af_a2f[3] = {0, 0, 0};
  float bf_b1f[3] = {0, 0, 0};
  float bf_b2f[3] = {0, 0, 0};
  float cf_c1f[3] = {0, 0, 0};
  float cf_c2f[3] = {0, 0, 0};

  // calculate rotated vectors a1f, a2f, b1f, b2f, c1f, c2f
  rotations(af_a1f, af_a1f_i, R_z_yaw, R_y_pitch, R_x_roll);
  rotations(af_a2f, af_a2f_i, R_z_yaw, R_y_pitch, R_x_roll);
  rotations(bf_b1f, bf_b1f_i, R_z_yaw, R_y_pitch, R_x_roll);
  rotations(bf_b2f, bf_b2f_i, R_z_yaw, R_y_pitch, R_x_roll);
  rotations(cf_c1f, cf_c1f_i, R_z_yaw, R_y_pitch, R_x_roll);
  rotations(cf_c2f, cf_c2f_i, R_z_yaw, R_y_pitch, R_x_roll);

  // calculate a1f, a2f, b1f, b2f, c1f, c2f
  float a1f[3] = {af[0] + af_a1f[0], af[1] + af_a1f[1], af[2] + af_a1f[2]};
  float a2f[3] = {af[0] + af_a2f[0], af[1] + af_a2f[1], af[2] + af_a2f[2]};
  float b1f[3] = {bf[0] + bf_b1f[0], bf[1] + bf_b1f[1], bf[2] + bf_b1f[2]};
  float b2f[3] = {bf[0] + bf_b2f[0], bf[1] + bf_b2f[1], bf[2] + bf_b2f[2]};
  float c1f[3] = {cf[0] + cf_c1f[0], cf[1] + cf_c1f[1], cf[2] + cf_c1f[2]};
  float c2f[3] = {cf[0] + cf_c2f[0], cf[1] + cf_c2f[1], cf[2] + cf_c2f[2]};

  // calculate vector a1 (from a10 to a1f), a2 (from a20 to a2f), b1 (from c10 to c1f), b2 (from b20 to b2f), c1 (from c10 to c1f), c2 (from c20 to c2f)
  float a1[3] = { a1f[0] - a10[0], a1f[1] - a10[1], a1f[2] - a10[2] };
  float a2[3] = { a2f[0] - a20[0], a2f[1] - a20[1], a2f[2] - a20[2] };
  float b1[3] = { b1f[0] - b10[0], b1f[1] - b10[1], b1f[2] - b10[2] };
  float b2[3] = { b2f[0] - b20[0], b2f[1] - b20[1], b2f[2] - b20[2] };
  float c1[3] = { c1f[0] - c10[0], c1f[1] - c10[1], c1f[2] - c10[2] };
  float c2[3] = { c2f[0] - c20[0], c2f[1] - c20[1], c2f[2] - c20[2] };


  //-------------------------
  //**STAGE 3 CALCULATIONS**
  // From {a1fx, a1fy, a1fz; a2fx, a2fy, a2fz; b1fx, b1fy, b1fz; b2fx, b2fy, b2fz; c1fx, c1fy, c1fz; c2fx, c2fy, c2fz}
  // => get {theta_a10, theta_a20, theta_b10, theta_b20, theta_c10, theta_c20}
  //-------------------------

  // save previous thetas
  for (int i = 0; i < 6; i++) {
    theta_prev[i] = theta[i];
  }

  // theta_a1
  float a1s_mod = abs(dot(a1, na)); // magnitude of vector 'a1s'
  float a1s[3] = { na[0] * a1s_mod, na[1] * a1s_mod, na[2] * a1s_mod }; 
  float a1_proj[3] = { a1[0] + a1s[0], a1[1] + a1s[1], a1[2] + a1s[2] }; // projection of vector 'a1' onto the ac plane
  float a1_proj_mod = mag(a1_proj); // magnitude of vector 'a1' projected on the ac plane
  float p2_proj_mod = sqrt(pow(p2, 2) - pow(a1s_mod, 2)); // magnitude of link p2 projected on the ac plane
  theta[0] = acos(dot(a1_proj, a_10_20) / (2 * d1 * a1_proj_mod ) );                                                    
  theta[0] = (theta[0] - acos((pow(a1_proj_mod, 2) + pow(p1, 2) - pow(p2_proj_mod, 2)) / (2 * a1_proj_mod * p1))) * toDeg;

  // theta_a2
  float a2s_mod = abs(dot(a2, na)); // magnitude of vector 'a2s'
  float a2s[3] = { na[0] * a2s_mod, na[1] * a2s_mod, na[2] * a2s_mod }; 
  float a2_proj[3] = { a2[0] + a2s[0], a2[1] + a2s[1], a2[2] + a2s[2] }; // projection of vector 'a2' onto the ab plane
  float a2_proj_mod = mag(a2_proj); // magnitude of vector 'a2' projected on the ab plane
  p2_proj_mod = sqrt(pow(p2, 2) - pow(a2s_mod, 2)); // magnitude of link p2 projected on the ab plane
  theta[1] = acos(-dot(a2_proj, a_10_20) / (2 * d1 * a2_proj_mod));                                                         
  theta[1] = (theta[1] - acos((pow(a2_proj_mod, 2) + pow(p1, 2) - pow(p2_proj_mod, 2)) / (2 * a2_proj_mod * p1))) * toDeg; 

  // theta_b1
  float b1s_mod = abs(dot(b1, nb)); // magnitude of vector 'b1s'
  float b1s[3] = { nb[0] * b1s_mod, nb[1] * b1s_mod, nb[2] * b1s_mod }; 
  float b1_proj[3] = { b1[0] + b1s[0], b1[1] + b1s[1], b1[2] + b1s[2] }; // projection of vector 'b1' onto the ab plane
  float b1_proj_mod = mag(b1_proj); // magnitude of vector 'b1' projected on the ab plane
  p2_proj_mod = sqrt(pow(p2, 2) - pow(b1s_mod, 2)); // magnitude of link p2 projected on the ab plane
  theta[2] = acos(dot(b1_proj, b_10_20) / (2 * d1 * b1_proj_mod));                                                         
  theta[2] = (theta[2] - acos((pow(b1_proj_mod, 2) + pow(p1, 2) - pow(p2_proj_mod, 2)) / (2 * b1_proj_mod * p1))) * toDeg; 
  
  // theta_b2
  float b2s_mod = abs(dot(b2, nb)); // magnitude of vector 'b2s'
  float b2s[3] = { nb[0] * b2s_mod, nb[1] * b2s_mod, nb[2] * b2s_mod }; 
  float b2_proj[3] = { b2[0] + b2s[0], b2[1] + b2s[1], b2[2] + b2s[2] }; // projection of vector 'b2' onto the cb plane
  float b2_proj_mod = mag(b2_proj); // magnitude of vector 'b2' projected on the cb plane
  p2_proj_mod = sqrt(pow(p2, 2) - pow(b2s_mod, 2)); // magnitude of link p2 projected on the cb plane
  theta[3] = acos(-dot(b2_proj, b_10_20) / (2 * d1 * b2_proj_mod));                                                         
  theta[3] = (theta[3] - acos((pow(b2_proj_mod, 2) + pow(p1, 2) - pow(p2_proj_mod, 2)) / (2 * b2_proj_mod * p1))) * toDeg; 
  
  // theta_c1
  float c1s_mod = abs(dot(c1, nc)); // magnitude of vector 'c1s'
  float c1s[3] = { nc[0] * c1s_mod, nc[1] * c1s_mod, nc[2] * c1s_mod }; 
  float c1_proj[3] = { c1[0] + c1s[0], c1[1] + c1s[1], c1[2] + c1s[2] }; // projection of vector 'c1' onto the cb plane
  float c1_proj_mod = mag(c1_proj); // magnitude of vector 'c1' projected on the cb plane
  p2_proj_mod = sqrt(pow(p2, 2) - pow(c1s_mod, 2)); // magnitude of link p2 projected on the cb plane
  theta[4] = acos(dot(c1_proj, c_10_20) / (2 * d1 * c1_proj_mod));                                                         
  theta[4] = (theta[4] - acos((pow(c1_proj_mod, 2) + pow(p1, 2) - pow(p2_proj_mod, 2)) / (2 * c1_proj_mod * p1))) * toDeg; 
  
  //theta_c2
  float c2s_mod = abs(dot(c2, nc)); // magnitude of vector 'c2s'
  float c2s[3] = { nc[0] * c2s_mod, nc[1] * c2s_mod, nc[2] * c2s_mod }; 
  float c2_proj[3] = { c2[0] + c2s[0], c2[1] + c2s[1], c2[2] + c2s[2] }; // projection of vector 'c2' onto the ac plane
  float c2_proj_mod = mag(c2_proj); // magnitude of vector 'c2' projected on the ac plane
  p2_proj_mod = sqrt(pow(p2, 2) - pow(c2s_mod, 2)); // magnitude of link p2 projected on the ac plane
  theta[5] = acos(-dot(c2_proj, c_10_20) / (2 * d1 * c2_proj_mod));                                                         
  theta[5] = (theta[5] - acos((pow(c2_proj_mod, 2) + pow(p1, 2) - pow(p2_proj_mod, 2)) / (2 * c2_proj_mod * p1))) * toDeg; 
  
  
  for (int i = 0; i < 6; i++) { 

    // change theta sign (negative up) 
    theta[i] = -theta[i];

    //checks theta values are between -40 and 40 degrees
    if (abs(theta[i]) > 40) {
      Serial.println("ERROR: CURRENT VALUES EXCEED ANGLE RANGE");
      Serial.println("Motor index:");
      Serial.println(i);
      Serial.println("Motor angle value:");
      Serial.println(theta[i]);
      stop();
    }

    //checks theta values are real numbers
    if (isnan(theta[i])) {
      Serial.println("ERROR: CURRENT VALUES CANNOT PHYSICALLY BE EXECUTED");
      Serial.println("Motor index:");
      Serial.println(i);
      Serial.println("Motor angle value:");
      Serial.println(theta[i]);
      stop();
    }

    //checks theta variation is smaller than 80 degrees
    if (abs(theta[i]-theta_prev[i]) > 80) {
      Serial.println("ERROR: CURRENT VALUES ARE TOO BIG FOR ONE STEP");
      Serial.println("Motor index:");
      Serial.println(i);
      Serial.println("Motor angle variation value:");
      Serial.println(theta[i]-theta_prev[i]);
      stop();
    }

  }
}

// compute rotations
void rotations(float* result, float hi[3], float Rz[3][3], float Ry[3][3], float Rx[3][3]) {
  float temp[3][3] = {{0, 0, 0}, {0, 0, 0}, {0, 0, 0}}; // Rz * Ry
  float combined[3][3] = {{0, 0, 0}, {0, 0, 0}, {0, 0, 0}}; // (Rz * Ry) * Rx

  // Compute Rz * Ry
  for (int i = 0; i < 3; i++) {
    for (int j = 0; j < 3; j++) {
      for (int k = 0; k < 3; k++) {
        temp[i][j] += Rz[i][k] * Ry[k][j];
      }
    }
  }

  // Compute (Rz * Ry) * Rx
  for (int i = 0; i < 3; i++) {
    for (int j = 0; j < 3; j++) {
      for (int k = 0; k < 3; k++) {
        combined[i][j] += temp[i][k] * Rx[k][j];
      }
    }
  }

  // Compute (Rz * Ry * Rx) * hi
  for (int i = 0; i < 3; i++) {
    result[i] = 0; // Initialize result
    for (int j = 0; j < 3; j++) {
      result[i] += combined[i][j] * hi[j];
    }
  }
}

//finds the magnitude of an array of size 3
float mag(float array[]) {  
  float mag = 0;
  for (int i = 0; i < 3; i++) {
    mag = mag + pow(array[i], 2);  //adds component i of array squared
  }
  mag = sqrt(mag);
  return mag;
}

//calculates the dot product of two arrays
float dot(float array1[], float array2[]) {  
  return array1[0] * array2[0] + array1[1] * array2[1] + array1[2] * array2[2];
}

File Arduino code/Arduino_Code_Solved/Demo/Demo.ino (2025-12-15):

/*               ****NOTES****
  Before using this, go to the Serial Settings
  tab in the Maestro Control Center and apply these settings:

   Serial mode: UART, fixed baud rate
   Baud rate: 9600
   CRC disabled

  Be sure to click "Apply Settings" after making any changes.

  Array Indexes
  -------------
  a1 = 0
  a2 = 1
  b1 = 2
  b2 = 3
  c1 = 4
  c2 = 5

  range for hz (105, 140)

*/

// libraries
#include "PololuMaestro.h"
#include "math.h"

#define maestroSerial SERIAL_PORT_HARDWARE_OPEN  //for teensy

// objects
MicroMaestro maestro(maestroSerial);  // if using the Maestro Micro controller


//**CONSTANTS**
//-------------
float abs_0 = 4000;                                     //ms position of absolute 0 degrees
float abs_90 = 8000;                                    //ms position of absolute 90 degrees
float toDeg = 180 / PI;                                 // radians to degrees conversion factor
int x = 0, y = 1, z = 2;                                // defines x, y, and z array indexes to be used
String ID[6] = { "a1", "a2", "b1", "b2", "c1", "c2" };  //servo ID's

//**USER DEFINED VALUES**
//----------------------

// angle range for each servo going CCW
// each servo can move from absolute 0 to absolute 90 degrees
// this defines a different range such as 90 to 180 degrees
float range[6][2] = { { -45, 45 }, { 45, -45 },  // a1, a2
                      { -45, 45 },
                      { 45, -45 },  // b1, b2
                      { -45, 45 },
                      { 45, -45 } };  // c1, c2

// angle offset value for each servo (should be less than 14 degrees since there are 25 teeth on the servo)
// redefines the position of the lower range of each servo
// Example: a servo with a range [0, 90] and an offset value of 5 would have its new 0 degree position where the old 5 degree position was

float offset[6] = { 0, 0,    // channel #0 and channel #1
                    0, 0,    // channel #2 and channel #3
                    0, 0 };  // channel #4 and channel #5

//**INVERSE KINEMATICS**
//----------------------

// user defined lengths (in mm)
float l0 = 73.025;
float lf = 67.775;
float d1 = 36.8893;
float d2 = 38.1;
float m = 12.7;
float p1 = 31.75;
float p2 = 129;

//calculates normal vectors nab, nac, and nbc for each side of the triangle
float nab[3] = { sqrt(3) * 0.5, -0.5, 0 };
float nac[3] = { sqrt(3) * 0.5, 0.5, 0 };
float nbc[3] = { 0, 1, 0 };

// intermediate variables
float t = (pow(lf, 2) * sqrt(3)) / 2;
float u = sqrt(pow(l0, 2) + pow(d1, 2)) * sin((2 * PI / 3) - atan(l0 / d1));  //(2*pi/3 is 120 degrees)

// calculates points a10, a20, b10, b20, c10, and c20
float a10[3] = { (d2 - u * sqrt(3)) / 2, (-u - d2 * sqrt(3)) / 2, 0 };
float a20[3] = { -a10[x], a10[y], 0 };
float b10[3] = { (u * sqrt(3) + d2) / 2, (d2 * sqrt(3) - u) / 2, 0 };
float b20[3] = { d2, u, 0 };
float c10[3] = { -b20[x], b20[y], 0 };
float c20[3] = { -b10[x], b10[y], 0 };

// calculates vectors, ab, ac, and bc
float ab[3] = { a20[x] - b10[x], a20[y] - b10[y], a20[z] - b10[z] };
float ac[3] = { a10[x] - c20[x], a10[y] - c20[y], a10[z] - c20[z] };
float bc[3] = { b20[x] - c10[x], b20[y] - c10[y], b20[z] - c10[z] };

float theta[6];                      //array for calculated theta values a1, a2, b1, b2, c1, c2 respectively
float nz = 1;                        //nz is predefined
float hz_norm = 118.19374266158451;  //normal hz value (at this height all servos are at 0 degrees)

void setup() {
  Serial.begin(115200);
  maestroSerial.begin(9600);
}

void loop() {
  //circle();
  //circulate();
  //while(1){}
  slowDemo();
  delay(1000);
  fastDemo();
  delay(1000);
  stop();
}


//Functions
void moveServo(int i, float pos, int spd, int acc) {        //moves servo i to an input position at a certain speed and acceleration value
  pos = pos + offset[i];                                    //adds offset amount to the input position
  pos = map(pos, range[i][0], range[i][1], abs_0, abs_90);  //converts input pos to ms position
  maestro.setSpeed(i, spd);                                 //sets input speed to servo i
  maestro.setAcceleration(i, spd);                          //sets input acceleration to servo i
  maestro.setTarget(i, pos);                                //drives motor to calculated position
}

void moveServos(int spd, int acc) {  //moves servos to their calculated positions at a certain speed and acceleration value
  float pos;
  for (int i = 0; i < 6; i++) {
    maestro.setSpeed(i, spd);                                 //sets input speed to servo i
    maestro.setAcceleration(i, acc);                          //sets input acceleration to servo i
    pos = theta[i] + offset[i];                               //adds offset amount to the calculated angle
    pos = map(pos, range[i][0], range[i][1], abs_0, abs_90);  //converts input pos to ms position
    maestro.setTarget(i, pos);                                //drives motor to calculated position
  }
}

void stop() {  //ends the program and stops all of the servos
  for (int i = 0; i < 6; i++) {
    maestro.setTarget(i, 0);  //stops servo i
  }
  while (1) {}
}
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
